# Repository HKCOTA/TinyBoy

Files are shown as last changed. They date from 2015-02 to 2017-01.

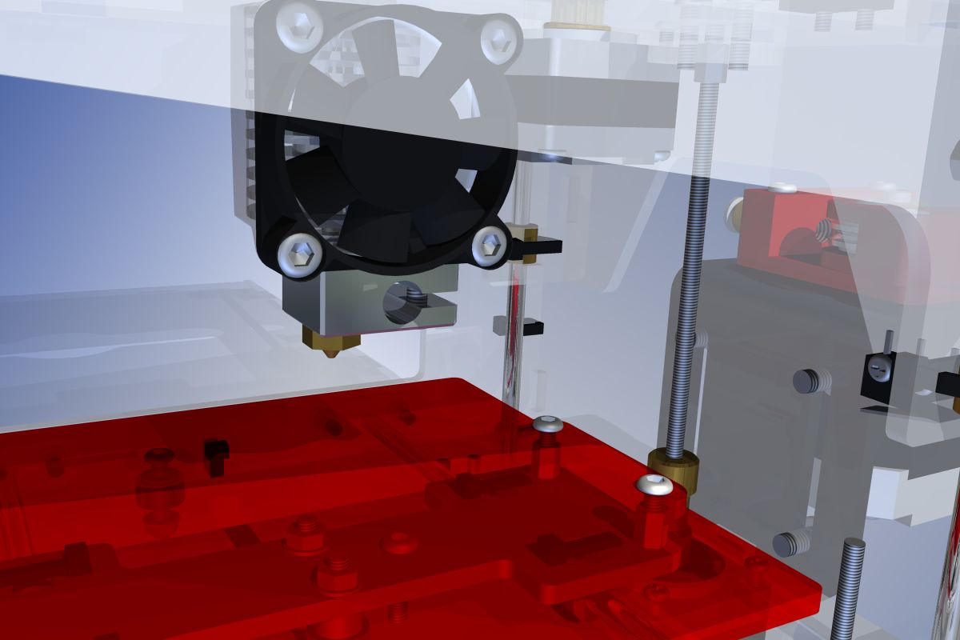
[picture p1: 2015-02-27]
photos/tinyboy_06.jpg

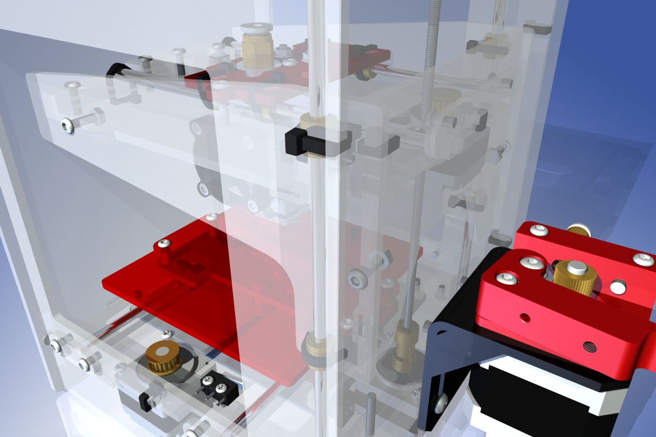
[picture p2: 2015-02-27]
photos/tinyboy_05.jpg

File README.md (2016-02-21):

# TinyBoy
A 3D Printer for Kids.

This repo are stored all the Blue Prints and design diagrams.
The TinyBoy design comes ABSOLUTELY NO WARRANTY!

TinyBoy by [Leung Chi-Wang (Parker Leung)](http://www.tinyboy.net) is licensed under a Creative Commons Attribution-ShareAlike 4.0 International License.  
To view a copy of this license, visit [http://creativecommons.org/licenses/by-sa/4.0/](http://creativecommons.org/licenses/by-sa/4.0/).  
Based on a work at [https://github.com/HKCOTA/TinyBoy](https://github.com/HKCOTA/TinyBoy).

CC-BY-SA means:
 1. Licensees may copy, distribute, display and perform the work and make derivative works based on it only if they give the author or licensor the credits in the manner specified by these.
 2. Licensees may distribute derivative works only under a license identical to the license that governs the original work. 

The TinyBoy design comes ABSOLUTELY NO WARRANTY!

### What is TinyBoy?
**TinyBoy - Open Design 3D Printer for Student  
A small , easy to build , affordable machine**

TinyBoy is an open design 3D printer. The size is just 15 x 15 x 22cm , even smaller than most of the 2D paper printer. Therefore , it fit for regular computer desk. The design aims as an entry-level machine for student and newbie to learn 3D modeling technology and train for creative thinking.

The project was started at 2011, and the first public demo was shown at the COSCUP, Taiwan 2013. [http://www.slideshare.net/noaizumi1/ss-25011267](http://www.slideshare.net/noaizumi1/ss-25011267)

TinyBoy won the First prize of the Innovation of the Best Teaching tools of the 29th China Adolescents Science & Technology Innovation Contest, 2014 (中国第29届全国青少年科技创新大赛 教师教具发明 一等奖) and the Best Innovation (Innovative Technology) Bronze Award of the Hong Kong ICT Awards 2015 (2105香港資訊及通訊科技獎:最佳創新(科技創新)獎銅獎).

TinyBoy is an open design 3D printer and you can get the details on our Github account (http://github.com/HKCOTA/TinyBoy) which is licensed under a Creative Commons Attribution-ShareAlike 4.0 International LicenseCC by SA.
To view a copy of this license, visit http://creativecommons.org/licenses/by-sa/4.0/.

Tinyboy 3D Printing Education Solution is a CCMF Grantees & Alumni of Hong Kong Cyberport Management Company Limited.

More Detail: [TinyBoy Website](http://www.tinyboy.net)
FaceBook: [https://www.facebook.com/tinyboy3dp](https://www.facebook.com/tinyboy3dp)

Supporting Organisation:
* [Hong Kong Creative Open Technology Association (HKCOTA)](http://cota.hk)
* [Opensource Hong Kong (OSHK)](http://opensource.hk)
* [Hong Kong Linux User Group (HKLUG)](http://www.linux.org.hk)

### Less is more

The maximum size of printed object is 8 x 8 x 8cm , which is relatively small than many other 3D printer. However, it is already large enough for making things like figure and toy.  

The gain from the trade off is the cost down of material and maintenance. Take out components for making large printed object , the design become simple and lean. The core material is acrylic sheet and connected by metal screw. Therefore , the cost of material and building can be minimized. 
The expect bill of material is just around ~USD$200.

### Easy to build / Learning by making

The process of making has the opportunity to transform education by inviting students to be something other than consumers of education. They can be maker of anything , moving from being directed to self-directed through the process. 

Tinyboy is designed for easy to build. The assemble from kit can be done by just using a screw driver. We wish student can make their own machine. Then they become a pioneer whose may make another one for other people. So that the use of 3D printer can be spread out to more student.

The case of Tinyboy uses acrylic plane as the main material. Individual parts can be made by using cutter laser. Therefore, the manufacturing process is easy once you have a laser cutter.  In fact , the price of an A5 laser cutter can be as cheap as USD $400. That make the cost of small amount production be reasonably low.

### Specification
* Size: 15cm(W) x 15cm(D) x 22cm(H) (excl. filament holder)  
* Printed size : 8cm x 8cm x 8cm  
* 1.75mm filament / 0.4mm hotend  

### Contributors
* Parker Leung (Chief Designer)
* TC Liu
* Wan Leung Wong
* Haggen So
* Henry Law
* Ben Lau (Honourable)

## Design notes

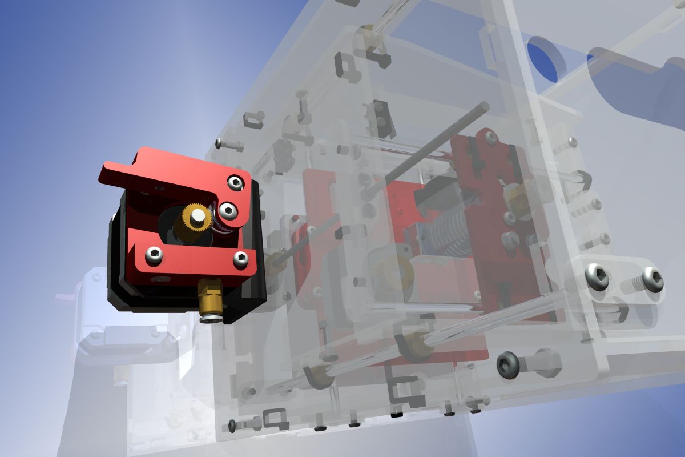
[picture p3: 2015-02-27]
photos/tinyboy_04.jpg

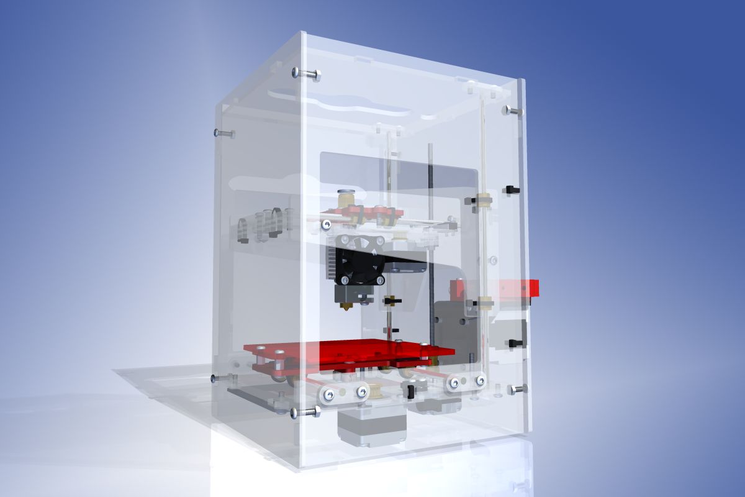
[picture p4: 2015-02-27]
photos/tinyboy_01.jpg

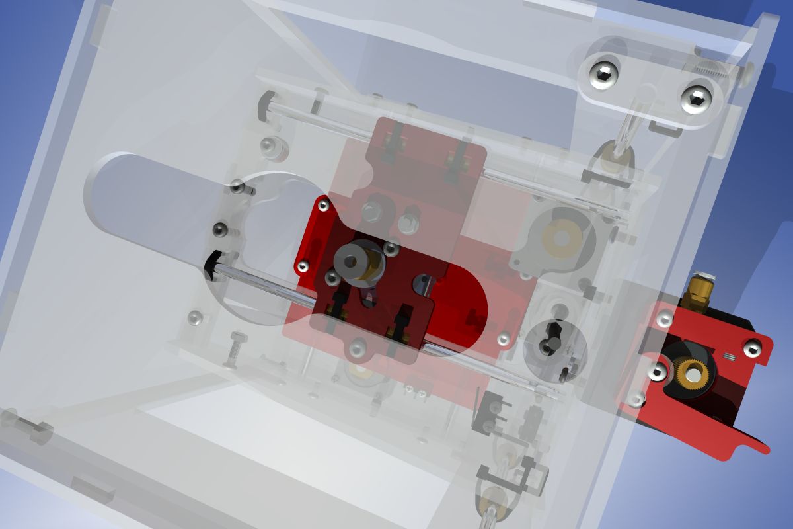
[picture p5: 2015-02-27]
photos/tinyboy_03.jpg

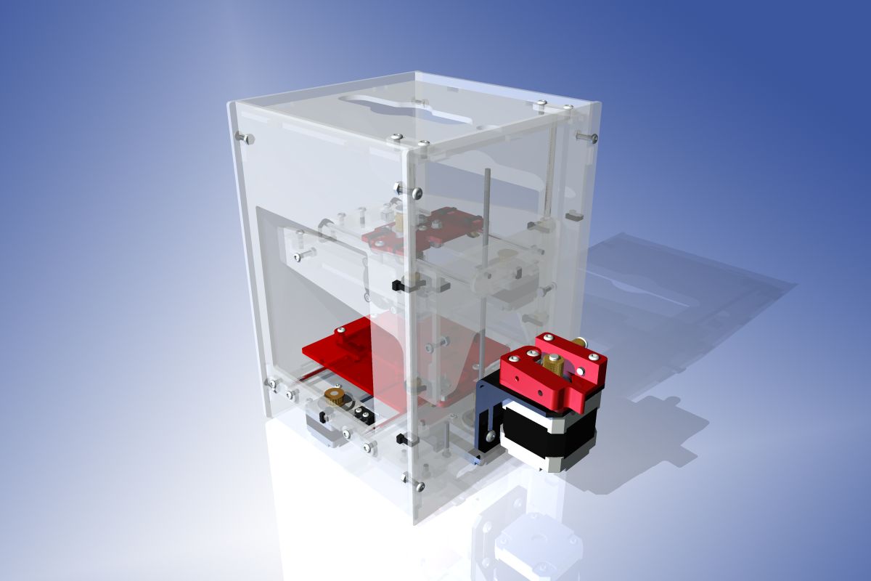
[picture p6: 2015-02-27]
photos/tinyboy_07.jpg

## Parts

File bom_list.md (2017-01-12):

Thanks dTom on helping to sort out the BOM List.

This BOM List is licensed under GPL.

Link: http://www.thingiverse.com/thing:880110

# Tinyboy BOM:

* lasercut acrylic 3mm x 1
<br><br>
* bearing 603zz x 6
* bearing 604uu (for extruder) x 1
* bearing LM4UU x 12
<br><br>
* Phillips head M2.5 5mm x 10
* Phillips head M2 8mm x 6
* Phillips head M3 5mm x 16
* hex screw M3 10mm x 15
* hex screw M3 12mm x 17
* hex screw M3 16mm x 5
* hex screw M3 22mm x 4
* hex screw M4 10mm x 2
* hex screw M4 8mm x 4
* threaded rod M3 180mm x 1
* M3 nut x 17
* M3 brass stud 6mm x 6
* M3 washer 70.5 x 16
* M3 washer 9*0.8 (for belt bearing) x 6
* M4 washer x 2
<br><br>
* rod 4mm 130mm x 2
* rod 4mm 140mm x 2
* rod 4mm 180mm x 2
<br><br>
* fastener 2.5mm x 22
<br><br>
* stepper_28 NEMA11 x 3
* stepper_42 NEMA17 (for extruder) x 1
* pulley MXL 16T x 2
* coupling 3mm x 3mm x 1
<br><br>
* timing belts MXL - 4mm x 1m (Y axis 43cm, X axis 47cm)
<br><br>
* mega2560 ramps1.4 with 4 A4988 stepstick x 1
* micro switch (for endstop) x 3
* extruder (mk8) x 1
* hot end e3dv6 x 1
* PTFE OD 4mm ID 2mm L 60cm x 1
* 12V 6A Transformer x 1

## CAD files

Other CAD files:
src/assembly base.iam
src/assembly extruder.iam
src/assembly x.iam
src/assembly y.iam
src/assembly z.iam
src/bearing_603zz.ipt
src/bearing_604uu.ipt
src/coupler_0305.ipt
src/e3d_v6.iam
src/e3d_v6_fan_duct.ipt
src/e3d_v6_heat_block.ipt
src/e3d_v6_heat_break.ipt
src/e3d_v6_heat_sink.ipt
src/e3d_v6_nozzle.ipt
src/extruder_base.ipt
src/extruder_gear.ipt
src/extruder_lever.ipt
src/extruder_spring.ipt
src/fan_3007.iam
src/fan_3007_base.ipt
src/fan_3007_blaze.ipt
src/fastener_01.ipt
src/fastener_02.ipt
src/fastener_03.ipt
src/fastener_04.ipt
src/nut_M3.ipt
src/nut_rod_M3_6.ipt
src/pc4_m10.ipt
src/pc4_m6.ipt
src/pcb_mks_1.ipt
src/plastic_part_00.ipt
src/plastic_part_01.ipt
src/plastic_part_02.ipt
src/plastic_part_03.ipt
src/plastic_part_04.ipt
src/plastic_part_05.ipt
src/plastic_part_06.ipt
src/plastic_part_11.ipt
src/plastic_part_12.ipt
src/plastic_part_13.ipt
src/plastic_part_21.ipt
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

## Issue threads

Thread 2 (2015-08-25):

Melting case

johnwhyte, 2015-08-25:
Hi, I really love your idea for a printer in each student desk. I think this design is great, but have some small areas which requires to be improved. I bought a printer with this design from HobbyKing website, and after one hour of use the case was melted.

I think the problem was that the acrylic plastic can hold temperatures up to 60 degrees without deforming or melting. But the stepper motors can reach more than 80 degrees (at least the specifications for the Nema 11 stepper says they can rise the temperature by 80 degrees).

In yout design the stepper motors for x and y axis are attached to the case using 3 screws. I think this needs to be changed and attach them by 4 screws. Ideally using some sort of metallic frame for the steppers, or not sure if some washers will suffice. Trying to distribute the heat in a big surface to avoid the deformation of the case.

noaizumi, 2015-08-26:
Hi, thanks for your concern. I m the designer of TinyBoy, basically we know the stepper can running up in high temperature and thats why we always choose good quality acrylic sheets (import from taiwan)  for building TinyBoy. We have build over 200+ machines, some of them running over 1000 hours and nil of them melted the case.

For the HobbyKing machine, we don't know what stepper and what plastic sheets they choose. Perhaps you can send this issue to they customer service and see they can give you a helping hand.

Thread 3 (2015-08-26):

x-axis

SirNorton, 2015-08-26:
I am having trouble with the x- axis  stepper motor jumping ,not belt,not to hot printer raised 20MM off table,it will be printing nice then for no apparent reason moves(jumps) about 1MM off . the stepper motor makes an evil noise at the moment it jumps. it is no way near the limits of travel when this happens. it is making me crazy.

noaizumi, 2015-08-27:
Hi, thanks for you reports. If you can run x/y/z normally by manual control, that means it won't be a circuit problems, most likely is a mechanic fault. Maybe you are running a bit higher current for your stepper, and cause too much heat accumulate, after a period of time it's too hot and the torque decrease cause missing step. However, in our experience, we don't likely occur this issue. Where is your stepper source come from? And you'd better check the current you use is it over the maximum current of the stepper.

SirNorton, 2015-08-27:
No in manual it is far worse

Sent from my HTC

----- Reply message -----
From: "noaizumi" <notifications@github.com>
To: "HKCOTA/TinyBoy" <TinyBoy@noreply.github.com>
Cc: "Frederick Douglas" <fcdnort@bellsouth.net>
Subject: [TinyBoy] x-axis  (#3)
Date: Thu, Aug 27, 2015 08:14

Hi, thanks for you reports. If you can run x/y/z normally by manual control, that means it won't be a circuit problems, most likely is a mechanic fault. Maybe you are running a bit higher current for your stepper, and cause too much heat accumulate, after a period of time it's too hot and the torque decrease cause missing step. However, in our experience, we don't likely occur this issue. Where is your stepper source come from? And you'd better check the current you use is it over the maximum current of the stepper.

&mdash;
Reply to this email directly or view it on GitHub.

wanleung, 2015-08-28:
It means that your x stepper had burn out.

SirNorton, 2015-08-28:
Had to stop in middle of print,x Scoville stepper motor has gotten so hot it is melting the plastic around the motor mount.,do I repair or will you in conjunction with hobby king get replacement parts to me. How's this work.

wanleung, 2015-08-31:
Sorry, We are NOT from HobbyKing. So you have to contact HobbyKing by yourself if your machine is bought from them. I am sorry.

We, HKCOTA, are a non-profit organization / charity (Reg.# 91/12580) in Hong Kong.
TinyBoy is an education project and the TinyBoy 3D printer is licensed under CC-BY-SA 4.0 and comes ABSOLUTELY NO WARRANTY.
A number of manufacturers are using the current design following CC-BY-SA to producing their own brand 3D printer. HobbyKing is one of them. We couldn't provide any support on the machines are not manufacturing by us.

For HKCOTA, we have our own small production line and is currently manufacturing small amount of the original TinyBoy 3D printer kit sets with high quality materials and parts (for children's good) for our education projects.

We are planning on shipping our kits to outside in the future,
please stick with us if you would like to order our kit set.

---
http://www.tinyboy.net/uncategorized/clarification-on-tinyboy-3d-printer-on-customer-support/

After we Open-Sourced the design of Tinyboy 3D Printer, more than one manufacturer commercialised the design and sold a good number of printers with their own channels. More education organisations and individuals can now afford Tinyboy and take advantage to this new technology.

On the other hand, the design of Tinyboy 3D printer is released under Creative Commons Attribution-Sharelike licence and many manufacturers legally made their own modifications to fit their target audiences. We are not aware of the details of those changes and may not be able to provide the best answers to specific questions.

Any comments that we made is offered in good faith to the best of our knowledge, but they cannot be regarded as a substitute for the official customer support offered by the manufacturers. Moreover, Tinyboy acts as a neutral body to all manufacturers and we did not receive any monetary compensation to provide customer support on behalf of any manufacturers.

LoyalNine1487, 2017-03-21:
If you look at the bottom of the printer their should be 4-5 Stepper drivers with a little screw like thing next to them. If you lose en the screw next to the letter "X" little bit  it should fix your problem.

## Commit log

2015-02-21 1st init
    [assembly base.iam, assembly extruder.iam, assembly x.iam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]
2015-02-27 new update
    [assembly base.iam, assembly extruder.iam, assembly y.iam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]
2015-03-03 Add donation button
2015-07-31 Update BOM List and Readme
2017-01-11 Update bom_list.md
    Added NEMA numbers for the steppers.
